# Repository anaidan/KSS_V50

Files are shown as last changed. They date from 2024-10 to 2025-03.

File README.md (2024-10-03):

Key Links
- [Design Spreadsheets, BOM, Power Budget](https://docs.google.com/spreadsheets/d/10r_KafIJN2HuMMp5E-dlICnizmNNihmT0PaAwAIZ1ew/edit?usp=sharing)
- [Mechanical CAD Model](https://cad.onshape.com/documents/6685182f6761d2ade72ba10d/w/25e23ac023e57743e67335a3/e/26fd2fa29841b9341751bee1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)

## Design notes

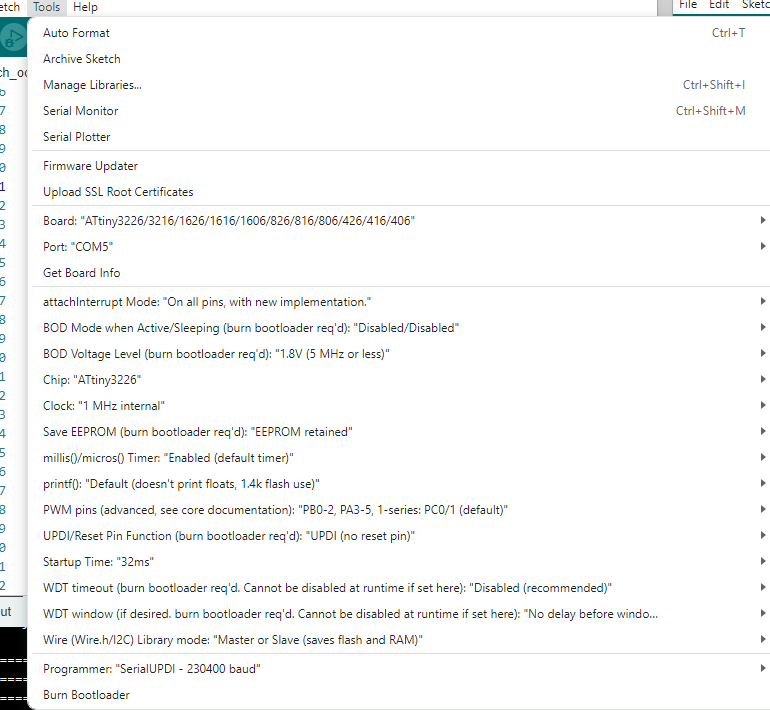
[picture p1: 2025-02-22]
FW/Screenshot 2025-02-22 114221.png

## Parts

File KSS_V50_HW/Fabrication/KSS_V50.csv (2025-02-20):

Designator | Value | DPN | Qty | DNP | JLC_PN | MPN | Dialectric
C5,C16,C17,C20,C25,C28,C29 | 10uF | 490-6473-1-ND | 7 |  | C237493 | GRM21BR61C106KE15K | X5R
C6,C12,C15 | 1uF | 311-1445-1-ND | 3 |  | C14664 | CC0603KRX5R8BB105 | X5R
C11,C13,C14,C18,C19,C21,C22,C23,C24,C26,C27,C30,C31,C34,C35,C36,C37,C38,C39,C40,C41 | 100nF | 311-1341-1-ND | 21 |  | C92490 | CC0603KRX7R8BB104 | X7R
C32 | 47nF | 311-1373-1-ND | 1 |  | C113811 | CC0603KRX7R8BB473 | X7R
C33 | 1nF | 311-3589-1-ND | 1 |  | C519404 | CC0603KRX7R8BB102 | X7R
D1 | NSR0520V2T1G | NSR0520V2T1GOSCT-ND | 1 |  | C99683 | NSR0520V2T1G
J1 | Conn_01x02_Socket | 455-1719-ND | 1 |  | C157932 | S2B-PH-K-S
J2,J3,J4,TP1,TP2 | -- mixed values -- |  | 5
J5 | Conn_01x07_Pin | 732-5340-ND | 1 |  |  | 61300711021
J7,J8 | Conn_01x04_Socket | WM7622CT-ND | 2 |  | C5119769 | 532610471
L2 | 2.2uH | 490-10607-1-ND | 1 |  | C882953 | DFE201610P-1R0M=P2
Q1,Q2,Q5 | DMG3414U-7 | DMG3414U-7DICT-ND | 3 |  | C260927 | DMG3414U-7
Q6 | SSM3J332R,LF | SSM3J332RLFCT-ND | 1 |  | C146367 | SSM3J332R,LF
R1,R10 | 50m | 273-KDV06DR050ETCT-ND | 2 |  | C5372686 | KDV06DR050ET
R2,R3 | 0 |  | 2 | DNP
R8,R9,R15,R16,R19,R20,R25,R26,R32 | 5.1 | YAG3372CT-ND | 9 |  | C114626 | RC0603FR-075R1L
R11 | 330 | 311-330HRCT-ND | 1 |  | C105881 | RC0603FR-07330RL
R12 | 2.2k | 311-2.20KHRCT-ND | 1 |  | C9900098075 | RC0603FR-072K2L
R13,R14 | 5Meg | 311-5.1MGRCT-ND | 2 |  | C141664 | RC0603JR-075M1L
R17 | 44.2k | 311-44.2KHRCT-ND | 1 |  | C95684 | RC0603FR-0744K2L
R18,R24,R41,R42,R43,R44,R45,R46,R47 | 10K | 311-10KLDCT-ND | 9 |  | C116677 | AC0603FR-0710KL
R21,R22,R23,R27,R28,R29,R33,R34,R35 | 1Meg | 311-1.00MHRCT-ND | 9 |  | C105578 | RC0603FR-071ML
R30,R31,R36,R37 | 5.1k | 311-5.10KHRCT-ND | 4 |  | C105580 | RC0603FR-075K1L
R38 | 470 | 311-470LDCT-ND | 1 |  | C144657 | AC0603FR-07470RL
SC1,SC2,SC3,SC4,SC5,SC6,SC7 | Solar_Cell | 2994-SM141K04TFS-ND | 7 | DNP |  | SM101K07L
SW2 | SW_SP3T | 563-1035-1-ND | 1 |  | C2921702 Copy | CS-4-13NTA
U1 | MAX40200AUK | MAX40200AUK+TCT-ND | 1 |  | C2649430 | MAX40200AUK+T
U2,U4 | INA236 | 296-INA236AIDDFRCT-ND | 2 |  | C5443912 | INA236AIDDFR
U3 | BQ29737 | 296-BQ29737DSERCT-ND | 1 |  | C3681751 | BQ29737DSER
U5 | TPS62843 | 595-TPS628438DRLR | 1 |  | C25838674 | TPS628438DRLR
U6,U8 | TMAG5328 | 296-TMAG5328A1DQDBVRCT-ND | 2 |  | C5220641 | TMAG5328A1DQDBVR
U7,U9 | TMC2300-LA-T | 175-TMC2300-LA-TCT-ND | 2 |  | C516356 | TMC2300-LA-T
U10 | ATtiny3226-X | 150-ATTINY3226-XF-ND | 1 |  | C3235640 | ATTINY3226-XF
U11 | AT42QT1010-TSHR | AT42QT1010-TSHRCT-ND | 1 |  | C74512 | AT42QT1010-TSHR
U12,U13,U14,U15 | SN74AUP1T34DCK | 296-34900-1-ND | 4 |  | C131985 | SN74AUP1T34DCKR

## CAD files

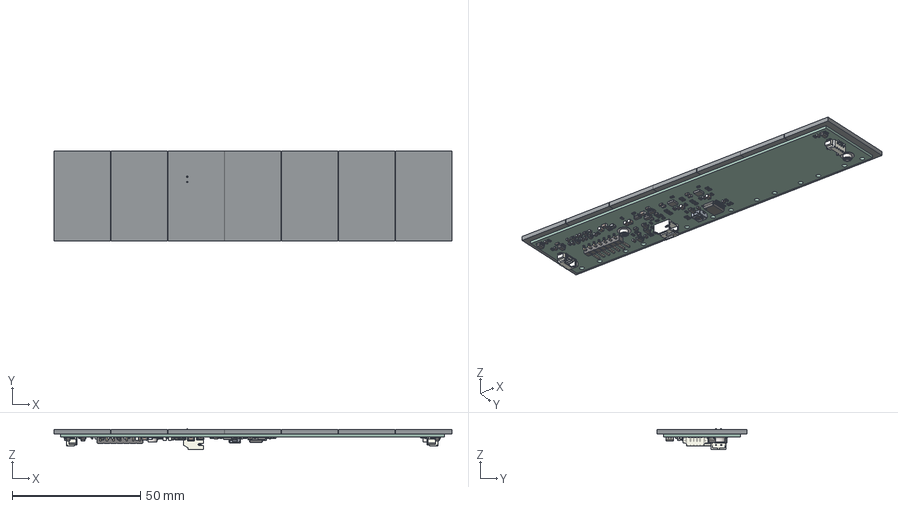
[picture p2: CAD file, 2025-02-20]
KSS_V50_HW/KSS_V50.step
154.9 x 35.0 x 8.25 mm
R_0603_1608Metric x 41
C_0603_1608Metric x 26
SOT_23_8 x 2
SOT_353_SC_70_5 x 4
C_0805_2012Metric x 7
WSON6_15x15mm_Pitch05mm
Molex_53261_0471 x 2
PinHeader_1x07_P254mm_Horizontal
SOT_563
1285AS-H-1R0M=P2
SOT_23_6 x 3
JST_S2B_PH_K
CS-4-13NTA
SOT-23-3 x 4
D_SOD_523
TMC2300-LA-T x 2
SSOP_20_53x72mm_P065mm
SOT_23_5
KSS_V50_PCB

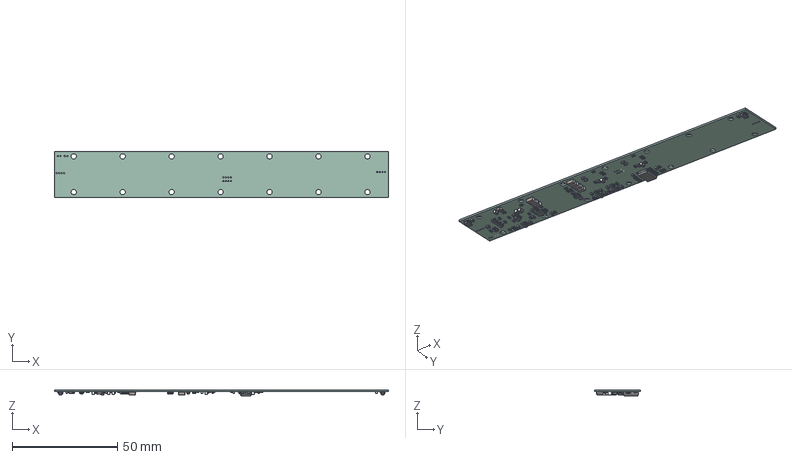
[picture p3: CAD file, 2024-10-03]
KSS_V50_Rev1/KSS_V50.step
159.0 x 21.7 x 2.95 mm
R_0603_1608Metric x 38
C_0603_1608Metric x 28
SOT_23_8 x 2
SOT_353_SC_70_5 x 4
C_0805_2012Metric x 6
C_1206_3216Metric x 7
WSON6_15x15mm_Pitch05mm
SOT_563
SOT_23_6 x 3
SOT-23-3 x 2
D_SOD_523
SSOP_20_53x72mm_P065mm
TSSOP_8_44x3mm_P065mm
KSS_V50_PCB

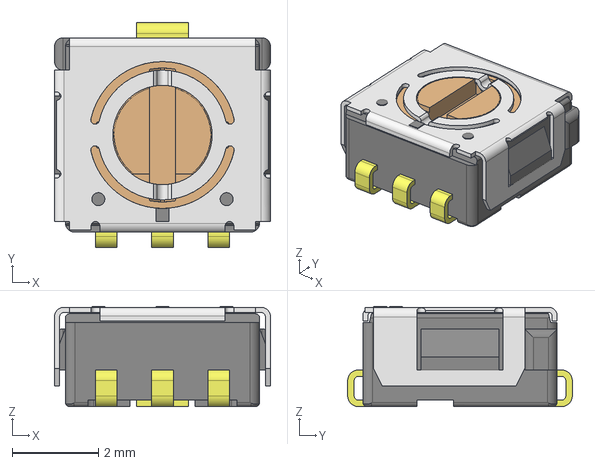
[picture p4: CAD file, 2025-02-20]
KSS_V50_HW/CS-4-13NTA.stp
5.00 x 5.20 x 2.32 mm
CS-4-13NA Body
CS-4-13NA7 Dial

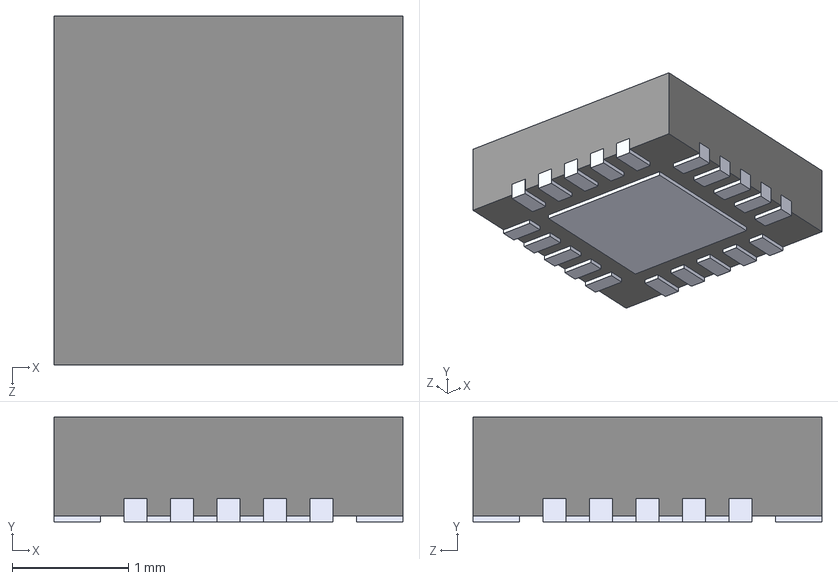
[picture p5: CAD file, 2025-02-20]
KSS_V50_HW/TMC2300-LA-T--3DModel-STEP-56544.STEP
3.00 x 0.9 x 3.00 mm

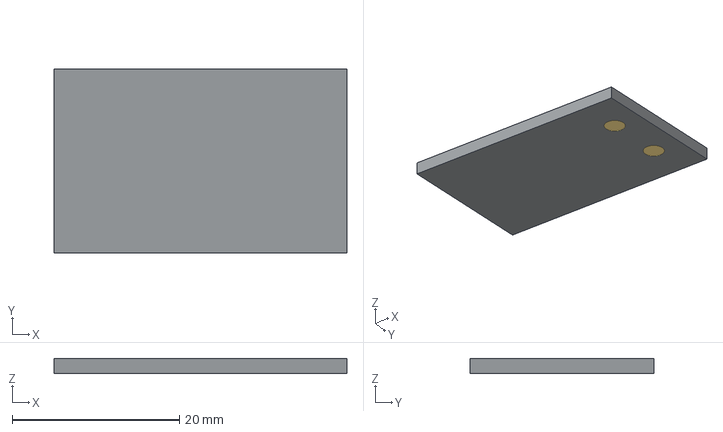
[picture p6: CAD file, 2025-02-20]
KSS_V50_HW/SM101K07L.step
35.0 x 22.0 x 1.80 mm

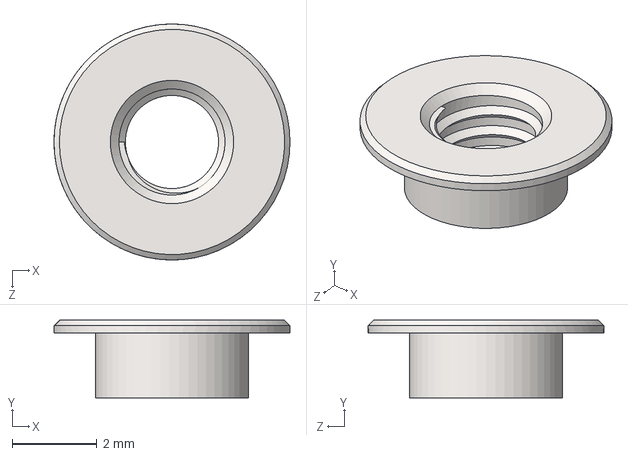
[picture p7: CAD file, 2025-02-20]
KSS_V50_HW/24929.STEP
5.56 x 1.83 x 5.56 mm

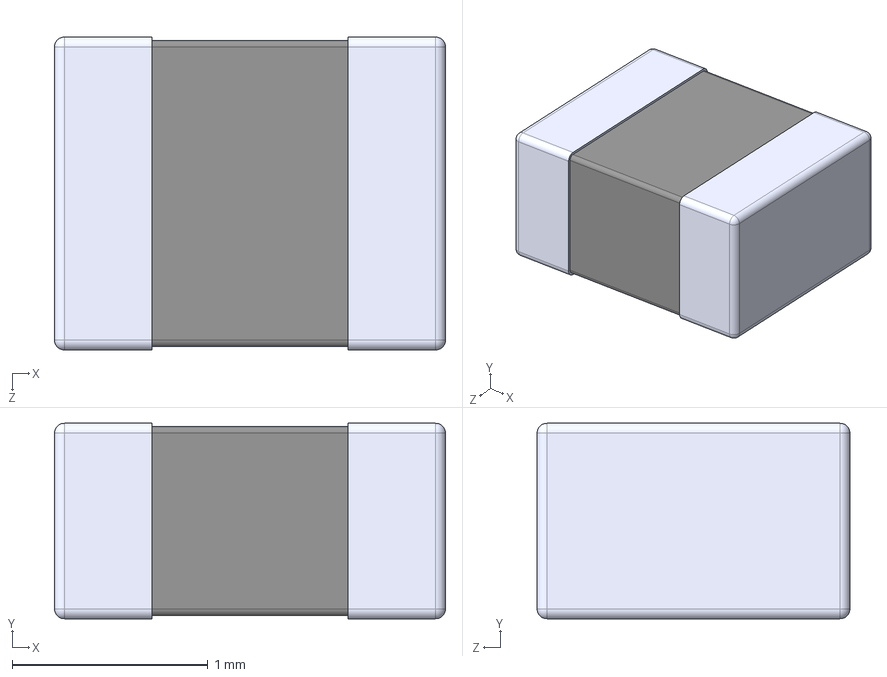
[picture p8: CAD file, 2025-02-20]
KSS_V50_HW/DFE201610P-1R0M_P2.step
2.00 x 1.00 x 1.60 mm

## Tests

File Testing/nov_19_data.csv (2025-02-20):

=~=~=~=~=~=~=~=~=~=~=~= PuTTY log 2024.11.18 21:14:29 =~=~=~=~=~=~=~=~=~=~=~=
3.9970.0400.7013.203
0.0610.0030.0000.000
3.9980.0500.7012.803
0.061-0.0030.0500.000
3.9980.0480.8013.203
0.0620.0000.0000.000
4.0000.0370.5513.203
0.0590.003-0.0500.000
3.9980.0320.6012.803
0.0610.0000.0000.000
3.9980.0600.8514.004
0.0580.000-0.0500.000
3.9970.0450.7512.803
0.061-0.003-0.0500.000
3.9970.0300.8012.803
0.061-0.003-0.0500.000
3.9970.0500.8513.203
0.0590.000-0.0500.000
3.9970.0350.8513.203
0.0590.0000.0500.000
3.9970.0350.7013.203
0.059-0.0050.0000.000
3.9980.0600.5513.203
0.059-0.0030.0000.000
3.9980.0520.9014.004
0.059-0.005-0.0500.000
3.9970.0370.7012.803
0.0610.0000.0000.000
3.9950.0350.7512.803
0.0590.003-0.0500.000
3.9980.0521.0014.004
0.0590.0000.0500.000
3.9970.0400.7012.803
0.059-0.003-0.0500.000
3.9980.0430.6512.803
0.059-0.0030.0500.000
4.0000.0570.9012.803
0.0610.0030.0500.000
3.9970.0401.0014.004
0.0610.003-0.0500.000
3.9970.0270.8012.803
0.0590.003-0.0500.000
3.9970.0480.5512.803
0.062-0.0050.0500.000
3.9980.0480.8013.203
0.0590.0000.0000.000
4.0000.0370.8012.002
0.0590.000-0.0500.000
3.9970.0370.7012.803
0.0590.000-0.0500.000
3.9980.0481.0013.203
0.0610.0030.0500.000
3.9970.0400.7512.002
0.0590.0000.0500.000
3.9970.0430.7012.803
0.061-0.0030.0000.000
3.9980.0521.0014.004
0.059-0.0050.0000.000
3.9970.0300.8013.203
0.061-0.0030.0000.000
3.9970.0320.6512.803
0.059-0.003-0.0500.000
3.9980.0500.8512.002
0.0610.000-0.0500.000
3.9980.0571.0014.004
0.0580.0000.0500.000
3.9970.0320.6513.203
0.0610.000-0.0500.000
3.9950.0350.5513.203
0.0610.0000.0000.000
3.9980.0500.9513.203
0.059-0.0030.0000.000
3.9970.0270.8012.002
0.0610.0000.0000.000
3.9980.0370.7512.002
0.0610.0000.0000.000
3.9970.0480.9013.203
0.059-0.0030.0000.000
3.9980.0220.6014.004
0.059-0.0030.0000.000
3.9950.0350.6513.203
0.058-0.0030.0000.000
3.9970.0521.1012.803
0.0610.000-0.0500.000
3.9980.0300.8514.004
0.0590.0000.0000.000
3.9970.0350.6512.803
0.0580.003-0.0500.000
3.9970.0430.6012.803
0.0610.0030.0000.000
3.9980.0480.7513.203
0.0590.003-0.0500.000
3.9970.0480.6513.203
0.0580.0000.0000.000
3.9970.0400.7013.203
0.061-0.003-0.1000.000
3.9980.0430.9514.004
0.058-0.0030.0000.000
3.9970.0350.7513.203
0.058-0.003-0.0500.000
3.9980.0370.7512.803
0.0580.0000.0000.000

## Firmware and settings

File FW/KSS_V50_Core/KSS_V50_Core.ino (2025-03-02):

#include <Wire.h>
#include <megaTinyCore.h>
#include <INA236.h>
#include <avr/sleep.h>
#include <avr/interrupt.h>


INA236 INA236_bat(0x40);
INA236 INA236_mppt(0x41);

#define MOT_STBY   PIN_PC3 

#define MOT_EN_1   PIN_PC1
#define MOT_STEP_1 PIN_PA3 
#define MOT_DIR_1  PIN_PA4
#define HALL_IN_1 PIN_PC0

#define MOT_EN_2   PIN_PA6
#define MOT_STEP_2 PIN_PA7
#define MOT_DIR_2  PIN_PB2
#define HALL_IN_2 PIN_PA5

#define MPPT_SHDN PIN_PB5
#define CAP_SNS_OUT PIN_PC2


volatile uint8_t minute_counter = 0;  // Keep track of elapsed minutes
volatile uint8_t hour_flag = 0;  
volatile uint8_t cap_sns_flag = 0;  

long step_1_cnt = 0;

long step_1_pos = 0;
long step_2_pos = 0; 

long max_pos = 3000;
long min_pos = 0;

int dir_1 = 0; // Towards panels
int dir_2 = 0; // towards panels

void setup() {

  pinMode_init();
  digitalWrite(MPPT_SHDN, LOW);

  Serial.pins(PIN_PA1, PIN_PA2);
  Serial.begin(9600);
  
  Wire.pins(PIN_PB1, PIN_PB0);
  Wire.begin();
  Wire.setClock(50000);

  INA236_bat.setMaxCurrentShunt(0.41, 0.050, false);
  INA236_mppt.setMaxCurrentShunt(0.41, 0.050, false);

  //printConfig(INA236_bat); 
  //printConfig(INA236_mppt); 

  TMC2300_enable();
  //measure(5, INA236_bat);
  //measure(5, INA236_mppt);
  TMC2300_disable();
  //measure(1, INA236_bat);
  //measure(5, INA236_mppt);

   ADC0.CTRLA &= ~ADC_ENABLE_bm;
   PORTC.PIN2CTRL = PORT_ISC_RISING_gc;
   RTC_init();
   sei();
   set_sleep_mode(SLEEP_MODE_PWR_DOWN);  /* Set sleep mode to POWER DOWN mode */
   sleep_enable();                       /* Enable sleep mode, but not going to sleep yet */
   sleep_cpu();
}

void loop() {
  
  set_sleep_mode(SLEEP_MODE_PWR_DOWN);  // Set sleep mode to POWER DOWN mode 
  sleep_enable();                       // Enable sleep mode, but not going to sleep yet
  sleep_cpu();

  sleep_disable();

  if(cap_sns_flag==1 || hour_flag==1){

    TMC2300_enable();

    //digitalWrite(MOT_DIR_1, HIGH);
    //digitalWrite(MOT_DIR_2, LOW);

    home();

    for(int i=0; i<30; i++){
      set_pos(random(-6000,40000), random(400,800), random(-6000,40000), random(400,800));
    }
    //set_pos(40000, 500, 40000, 500);
    //Serial.println(step_1_pos);
    //Serial.println(step_2_pos);
    //delay(3000);
    set_pos(0, 500, 0, 500);
    //home();

    Serial.println(digitalRead(HALL_IN_1));
    Serial.println(digitalRead(HALL_IN_2));

    TMC2300_disable();

    if(cap_sns_flag==1 || hour_flag==1){
      cap_sns_flag = 0;
      hour_flag = 0;
    }

    /*if(digitalRead(HALL_IN_1)==0){
      digitalWrite(MOT_DIR_1, LOW);
      Serial.println("end stop");
      step_1_cnt = 0;
      
    }

    if(step_1_cnt > 2000){
      digitalWrite(MOT_DIR_1, HIGH);    
      Serial.println("reverse");
    }*/

  }



}

void home(){

  digitalWrite(MOT_DIR_1, LOW);
  digitalWrite(MOT_DIR_2, HIGH);

  step_motors(80000, 200, 0); // away from hall

  digitalWrite(MOT_DIR_1, HIGH);
  digitalWrite(MOT_DIR_2, LOW);

  step_motors(80000, 200, 1); // towards hall

  step_1_pos = 0;
  step_2_pos = 0;
  set_pos(0, 500, 17000, 200); //offset
  step_1_pos = 0;
  step_2_pos = 0;  

}

void step_motors(long step_cnt, long speed, int towards){
    for(int i=0; i<step_cnt; i++){
      
      digitalWrite(MOT_STEP_1, LOW);
      digitalWrite(MOT_STEP_2, LOW);

      delayMicroseconds(speed);
      
      if(digitalRead(HALL_IN_1)!=0 && towards==1){
        digitalWrite(MOT_STEP_1, HIGH);
      }
      else if(digitalRead(HALL_IN_1)!=1 && towards==0){
        digitalWrite(MOT_STEP_1, HIGH);
      }

      if(digitalRead(HALL_IN_2)!=0 && towards==1){
        digitalWrite(MOT_STEP_2, HIGH);
      }
      else if(digitalRead(HALL_IN_2)!=1 && towards==0){
        digitalWrite(MOT_STEP_2, HIGH);
      }      
      
      delayMicroseconds(speed);

      if(digitalRead(HALL_IN_1)==0 && digitalRead(HALL_IN_2)==0 && towards==1){
        break;
      }
      else if(digitalRead(HALL_IN_1)==1 && digitalRead(HALL_IN_2)==1 && towards==0){  
        break;
      }
    }  
}

void set_pos(long set_point_1, long speed_1, long set_point_2, long speed_2){
  if(set_point_1>step_1_pos){
    digitalWrite(MOT_DIR_1, LOW);
    dir_1 = 1;
  }
  else{
    digitalWrite(MOT_DIR_1, HIGH);
    dir_1 = -1;
  }

  if(set_point_2>step_2_pos){
    digitalWrite(MOT_DIR_2, HIGH);
    dir_2 = 1;
  }
  else{
    digitalWrite(MOT_DIR_2, LOW);
    dir_2 = -1;
  }  

  long current_time  = micros();
  long prev_time_1   = micros();
  long prev_time_2   = micros();


  while((labs(set_point_1-step_1_pos)>10) || (labs(set_point_2-step_2_pos)>10)){
    
    current_time = micros();
    
    if((current_time - prev_time_1) >= speed_1 && (labs(set_point_1-step_1_pos)>10)){
      digitalWrite(MOT_STEP_1, HIGH);
      step_1_pos+=dir_1;
      prev_time_1 = current_time;
      delayMicroseconds(10);
    }
    digitalWrite(MOT_STEP_1, LOW);

    current_time = micros();

    if((current_time - prev_time_2) >= speed_2 && (labs(set_point_2-step_2_pos)>10)){
      digitalWrite(MOT_STEP_2, HIGH);
      step_2_pos+=dir_2;
      prev_time_2 = current_time;
      delayMicroseconds(10);
    }
    digitalWrite(MOT_STEP_2, LOW);
  }

  Serial.println(labs(set_point_1-step_1_pos));
  Serial.println(labs(set_point_2-step_2_pos));


}

ISR(PORTC_PORT_vect) {
    // Clear the interrupt flag
    PORTC.INTFLAGS = CAP_SNS_OUT;
    cap_sns_flag = 1; 
}

// RTC PIT Interrupt Service Routine (fires every minute)
ISR(RTC_PIT_vect) {
    RTC.PITINTFLAGS = RTC_PI_bm;  // Clear interrupt flag

    minute_counter++;
    if (minute_counter >= 10) {  // 60 minutes = 1 hour
        minute_counter = 0;
        hour_flag = 1;
    }
}

void RTC_init(){
  while (RTC.STATUS > 0);  // Wait for synchronization
  
  // Enable the internal 32.768kHz oscillator for RTC
  RTC.CLKSEL = RTC_CLKSEL_INT32K_gc;

  // Enable RTC PIT with a 1-minute interval
  //RTC.PITCTRLA = RTC_PERIOD_CYC32768_gc | RTC_PITEN_bm;  // 64-second tick
  RTC.PITCTRLA = RTC_PERIOD_CYC32768_gc | RTC_PITEN_bm;  // 1-second tick
  RTC.PITINTCTRL = RTC_PI_bm;  // Enable periodic interrupt

}

void printConfig(INA236 INA)
{
  Serial.print("LSB:\t");
  Serial.println(INA.getCurrentLSB(), 10);
  Serial.print("LSB_uA:\t");
  Serial.println(INA.getCurrentLSB_uA(), 3);
  Serial.print("shunt:\t");
  Serial.println(INA.getShunt(), 3);
  Serial.print("maxCur:\t");
  Serial.println(INA.getMaxCurrent(), 3);
  Serial.println();
}

void measure(uint8_t count, INA236 INA)
{
  // delay(3000);
  Serial.println("\nBUS\tSHUNT\tCURRENT\tPOWER");
  Serial.println(" V\t mV\t mA\t mW");
  for (int i = 0; i < count; i++)
  {
    Serial.print(INA.getBusVoltage(), 3);
    Serial.print("\t");
    Serial.print(INA.getShuntVoltage_mV(), 3);
    Serial.print("\t");
    Serial.print(INA.getCurrent_mA(), 3);
    Serial.print("\t");
    Serial.print(INA.getPower_mW(), 3);
    Serial.println();
    delay(100);
  }
}

void INA236_log(INA236 INA_bus, INA236 INA_mppt){
  Serial.print(INA_bus.getBusVoltage(), 3);
  Serial.print("\t");
  Serial.print(INA_bus.getShuntVoltage_mV(), 3);
  Serial.print("\t");
  Serial.print(INA_bus.getCurrent_mA(), 3);
  Serial.print("\t");
  Serial.print(INA_bus.getPower_mW(), 3);
    
  Serial.println();  
  
  Serial.print(INA_mppt.getBusVoltage(), 3);
  Serial.print("\t");
  Serial.print(INA_mppt.getShuntVoltage_mV(), 3);
  Serial.print("\t");
  Serial.print(INA_mppt.getCurrent_mA(), 3);
  Serial.print("\t");
  Serial.print(INA_mppt.getPower_mW(), 3);

  Serial.println();  

}

void TMC2300_enable(){
  // Bring all MCU outputs low interfacing with motor driver, VIO/STBY ON
  digitalWrite(MOT_STEP_1, LOW);
  digitalWrite(MOT_STEP_2, LOW);
  //digitalWrite(MOT_DIR_1, HIGH);
  //digitalWrite(MOT_DIR_2, LOW);
  digitalWrite(MOT_EN_1, LOW);
  digitalWrite(MOT_EN_2, LOW);
  delay(5);
  
  // Turn VIO/STBY OFF
  digitalWrite(MOT_STBY, HIGH);
  delay(5);
  
  // Turn VIO/STBY ON
  digitalWrite(MOT_STBY, LOW);
  delay(500);
  
  // Turn Enables ON
  digitalWrite(MOT_EN_1, HIGH);
  digitalWrite(MOT_EN_2, HIGH);
  delay(5);
}

void TMC2300_disable(){
  // Bring all MCU outputs low interfacing with motor driver, VIO/STBY ON
  digitalWrite(MOT_STEP_1, LOW);
  digitalWrite(MOT_STEP_2, LOW);
  digitalWrite(MOT_DIR_1, LOW);
  digitalWrite(MOT_DIR_2, LOW);
  digitalWrite(MOT_EN_1, LOW);
  digitalWrite(MOT_EN_2, LOW);
  delay(5);
  
  // Turn VIO/STBY OFF
  digitalWrite(MOT_STBY, HIGH);
}

void pinMode_init(){
  pinMode(CAP_SNS_OUT, INPUT);
  pinMode(MOT_STBY, OUTPUT);
  pinMode(CAP_SNS_OUT, INPUT);
  
  pinMode(MOT_EN_1, OUTPUT);   
  pinMode(MOT_STEP_1, OUTPUT);  
  pinMode(MOT_DIR_1, OUTPUT);   
  pinMode(HALL_IN_1, INPUT);

  pinMode(MOT_EN_2, OUTPUT);    
  pinMode(MOT_STEP_2, OUTPUT);  
  pinMode(MOT_DIR_2, OUTPUT);  
  pinMode(HALL_IN_2, INPUT);

  pinMode(MPPT_SHDN, OUTPUT);
}

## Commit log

2024-10-03 files i've been working on for a while
    [2_5V_Buck_Boost.kicad_sch, Battery_Protection.kicad_sch, KSS_V50.kicad_pcb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]
2025-02-20 post assembly commit
    [24929.STEP, 2_5V_Buck_Boost.kicad_sch, Battery_Protection.kicad_sch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]
2025-02-22 basic arduino code sleep setup
2025-02-22 Cap sense interrupt working
2025-02-22 RTC/PIT interrupt working
2025-03-01 homing crash fixed by adding delay after PFET turn ON
    [2_5V_Buck_Boost.kicad_sch, Battery_Protection.kicad_sch, KSS_V50.kicad_sch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]
2025-03-02 Working random setpoint test
    [KSS_V50.kicad_pcb]
2025-03-02 Added better homing for edge detection

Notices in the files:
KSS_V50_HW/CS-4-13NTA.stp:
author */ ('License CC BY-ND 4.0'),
